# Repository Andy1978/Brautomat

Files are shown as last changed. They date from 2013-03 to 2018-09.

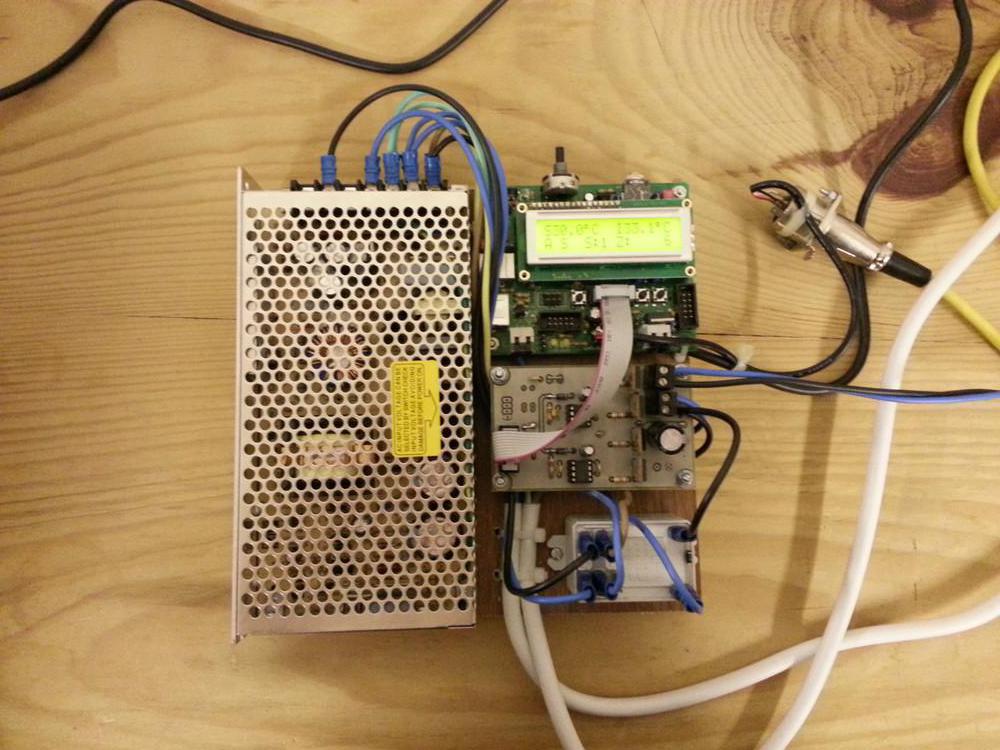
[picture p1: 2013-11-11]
images/detail_ansteuerung.jpg

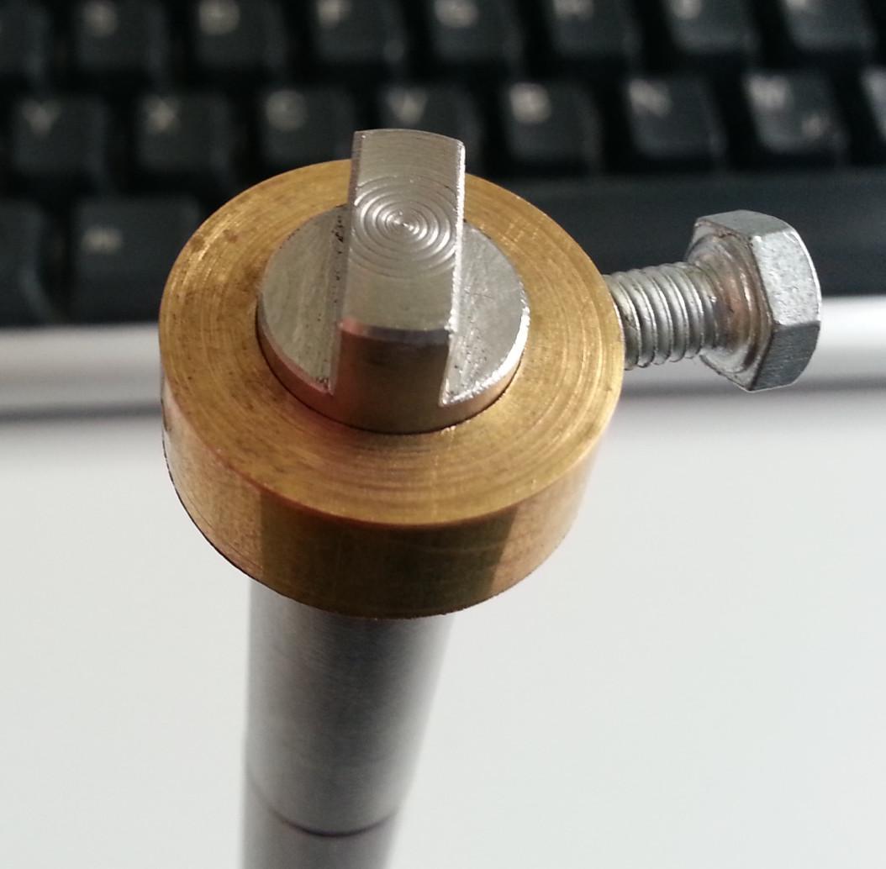
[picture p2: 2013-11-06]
images/edelstahlwelle_zapfen.jpg

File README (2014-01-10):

Brautomat - der (Bier)brau(au)tomat

Funktionen:
  * Ansteuerung des Rührwerks mit konstanter Drehzahl oder Sinusmodulation für maximale Durchmischung
  * Temperaturregelung entlang des konfigurierbaren Profils.

Schaltplände und Stückliste finden sich in /Dokumentation, CAD Zeichnungen kommen noch dazu.
Als  Basis dient YAAMB https://github.com/YAAMB/YAAMB

Bilder finden sich im wiki https://github.com/Andy1978/Brautomat/wiki

ToDo:
  * Wiki strukturieren, Bilder vom Brauprozess
  * CAD Zeichnungen hinzufügen
  * Identifikation der Streckenparameter, siehe playground
  * 2 Punkt Regler in der Software durch quasi kontinuierlichen Regler mit PWM Modulation ersetzen, P oder PI Regler verwenden
  * Neue monolithische Platine mit den wichtigen Komponenten und günstigerer USB<->serial Wandler

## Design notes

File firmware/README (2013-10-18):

*** Brautomat ***

Andreas Weber:
Firmware für den Atmega32 mit MKBoard.
Ich verwende vorerst bei Board mit der HardwareRev1

fuses sind
avrdude -P usb -c usbasp -p atmega32 -U lfuse:w:0x3F:m
avrdude -P usb -c usbasp -p atmega32 -U hfuse:w:0xD9:m

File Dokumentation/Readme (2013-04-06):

02.03.2013 Andreas Weber

Bitte keine Dokumente hinzufügen, für die wir nicht die Rechte haben. Bitte nur verlinken

Atmega32 Datenblatt: www.atmel.com/Images/doc2503.pdf

PT100 Diskussionen
http://www.mikrocontroller.net/topic/183991 (dort von MaWin)
http://groups.google.de/group/de.sci.electronics/browse_thread/thread/6f4a76565e833cb4/6aa603074f212afd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

Nur ganz grobe Werte. (später über Polynom berechnen)
0°C   100R
20°C  108R
100°C 138R

Application Notes:
Precision RTD Instrumentation for Temperature Sensing http://ww1.microchip.com/downloads/en/AppNotes/01154a.pdf ***
Precision Temperature Sensing With RTD Circuits (AN687) ww1.microchip.com/downloads/en/appnotes/00687c.pdf

Für den DS18X20:
http://gandalf.arubi.uni-kl.de/avr_projects/tempsensor/

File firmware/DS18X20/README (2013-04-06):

6.4.2013 Andreas Weber

DS18X20 Library from Martin Thomas
http://www.siwawi.arubi.uni-kl.de/avr_projects/tempsensor/

Makefile und main quick&dirty angepasst für MKBoard und avrdude.

Beispiel hier dient zum auslesen der Seriennummer,
beim ersten gebauten Brautomat (Sensor von Klaus)
SN: 5A F2 BD 04 00 00

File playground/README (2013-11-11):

07.11.2013 Andreas Weber
Spielerei mit octave control

Links:
http://wiki.octave.org/Control_package
http://octave.sourceforge.net/control/index.html
http://web.mit.edu/6.302/www/compare/report.html
http://www.frad.t.u-tokyo.ac.jp/~miyoshi/nu2006/octave-doc-2.1.35/octave_29.html#SEC176

http://www.mathworks.de/de/help/control/index.html

hm, test_control zeigt 2 failed tests.. mal bugreport schreiben?

L = tf(3e4 * [0.0025 0.1 1], [0.01 1.03 3.03 3.01 1]);

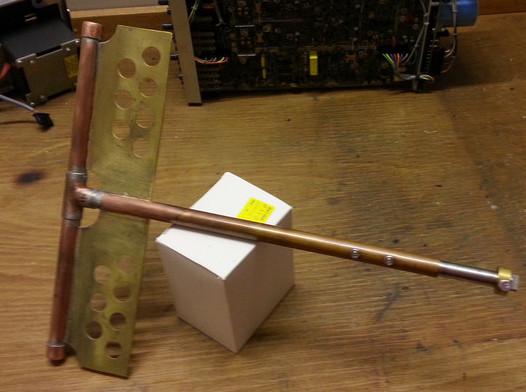
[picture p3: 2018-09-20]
images/ruehrwerk.jpg

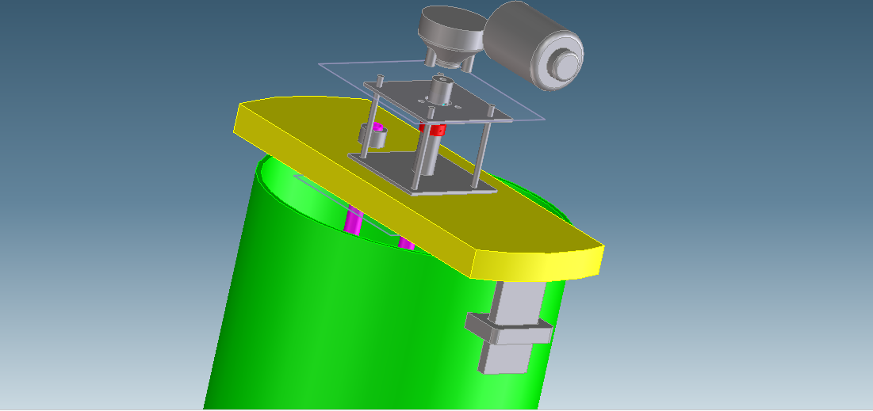
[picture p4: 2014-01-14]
images/cad_detail_motor2.png

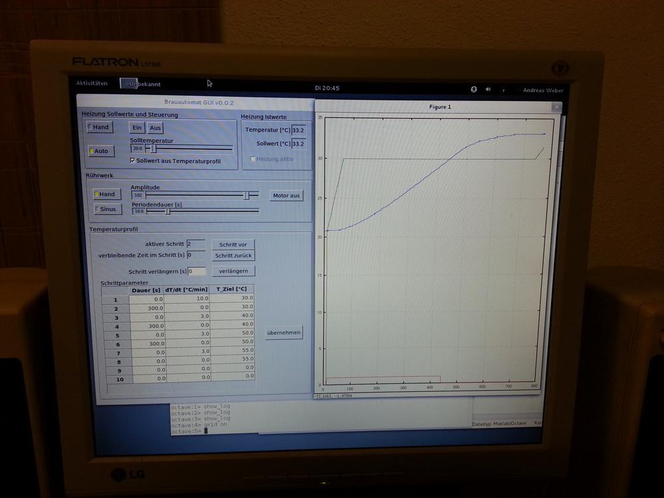
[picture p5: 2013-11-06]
images/screenshot.jpg

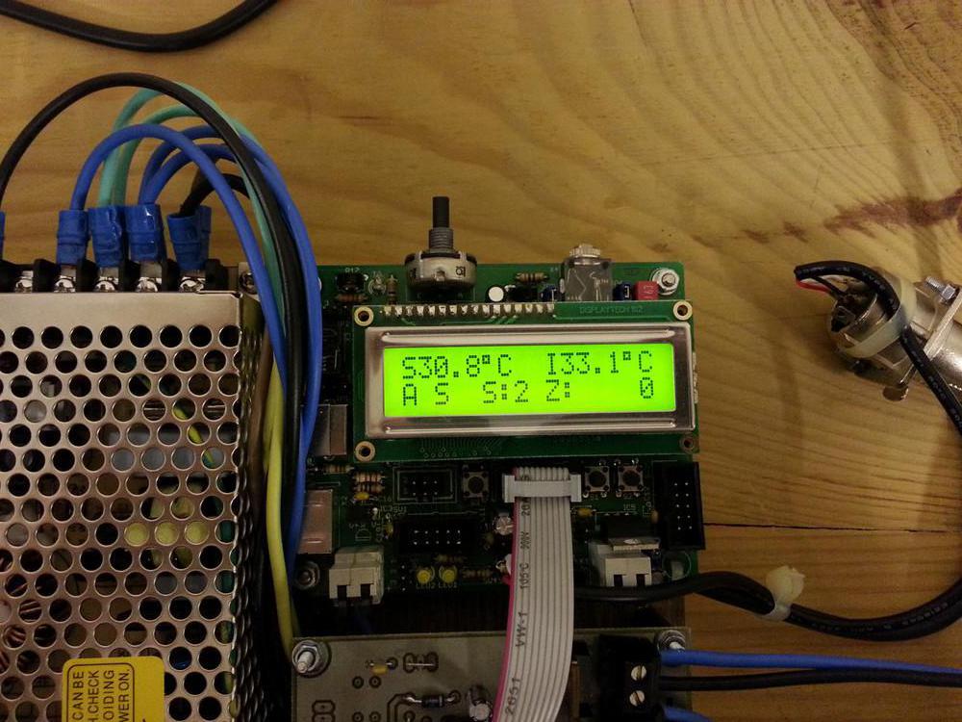
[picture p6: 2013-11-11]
images/detail_lcd.jpg

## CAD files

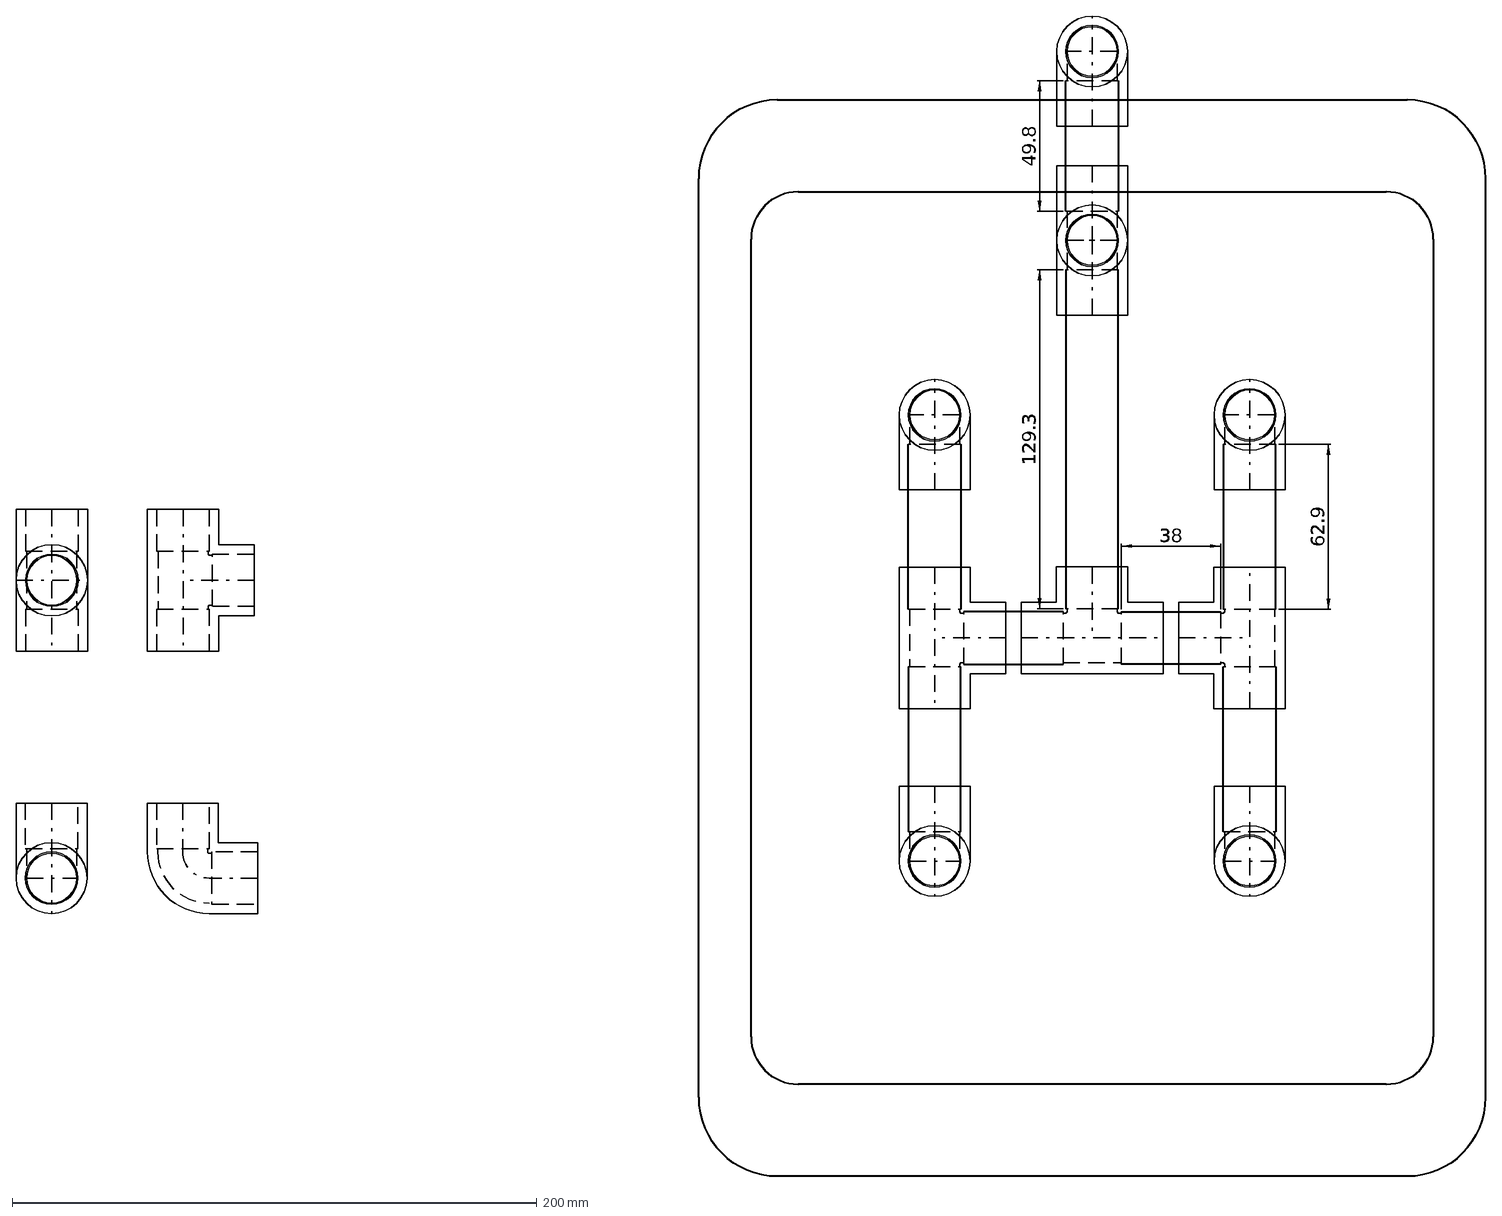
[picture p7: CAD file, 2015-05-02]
CAD/spuelomat.dxf
62.9
38
129.3
49.8

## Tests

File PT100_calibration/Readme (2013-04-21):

19.04.2013 Andreas Weber

Test programs and scripts to test the PT100-wheatstone bridge setup
on AVR differential inputs.

##                               ___    |
##                           5V -UUU----oAVcc
##                                      |
##  .----o--------------o---------------oARef
##  |    |              |               |
##  |   .-.            .-.              |
##  |   | | R1         | | R2           |
##  |   | | 6.8k       | | 6.8k         |
##  |   '-'            '-'              |
##  |    |              |               |
##  |    o--------------)---------------oADC 0
## ---   |              |               |
## ---   |              o---------------oADC 1
##  |    |              |               |
## 100nF |              |               |
##  |   .-.            .-.              |
##  |   | | Rpt        | | R3           |
##  |   | | PT100      | | 120R         |
##  |   '-'            '-'              |
##  |    |              |               |
##  '----o--------------o---------------oAGND
##                                      |
##(created by AACircuit v1.28.6 beta 04/19/05 www.tech-chat.de)

put both sensors (PT100 and DS18B20) into boiling water, run pt100cal with
./pt100cal | tee yourlogfile.log

log the temperature decreasing and then process it in octave

captures/100deg_1.log.gz
  was a first fast polling measurement without timestamp
  and suffered from a int16 overflow (sum filter was too big)

captures/100deg_2.log 
  second capture with temperatures from 95°C .. -5°C (ice and salt)
  huber_D150_2.log is the corresponding, manual captured reference

captures/100deg_3.log 
  third capture in isolated mug and temperatures from 95°C..13.3°C
  huber_D150_3.log is the corresponding, manual captured reference

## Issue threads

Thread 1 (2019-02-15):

Feature Request: Heating-Status-LED and Beep-Sound

Tilogorn, 2019-02-15:
Hi Andy,

i really love your brew automation software! I recently made my first wort with it. Two things would have helped to improve comfort a little:

- would it be possible to get a status LED in the gui, which displays the current state of the heating relay?
- would it be possible to get a beep-sound when the target temperature was reached the first time?

Unfortunately I'm just a webdev and can't create a PR. But be sure to taste one of my "products" some day ;-)

Thanks in advance!
Daniel

Andy1978, 2019-02-15:
There is a checkbox "Heizung aktiv" in the upper right corner which should show the state of the relay. Doesn't work this for you?

For the beep I think we can add some command in the config file which is executed as soon as the temperature is reached. So you can add something as "aplay foobar.wav"
 or "mplayer foobar.mp3"

Tilogorn, 2019-02-19:
> There is a checkbox "Heizung aktiv" in the upper right corner which should show the state of the relay. Doesn't work this for you?

That's exactly what I was looking for. I am blind sometimes. Thanks a lot.

> For the beep I think we can add some command in the config file which is executed as soon as the temperature is reached. So you can add something as "aplay foobar.wav"
> or "mplayer foobar.mp3"

Sounds like a very flexible solution!. One can play sounds, send mails, set GPIOs (Rpi) or whatever ...

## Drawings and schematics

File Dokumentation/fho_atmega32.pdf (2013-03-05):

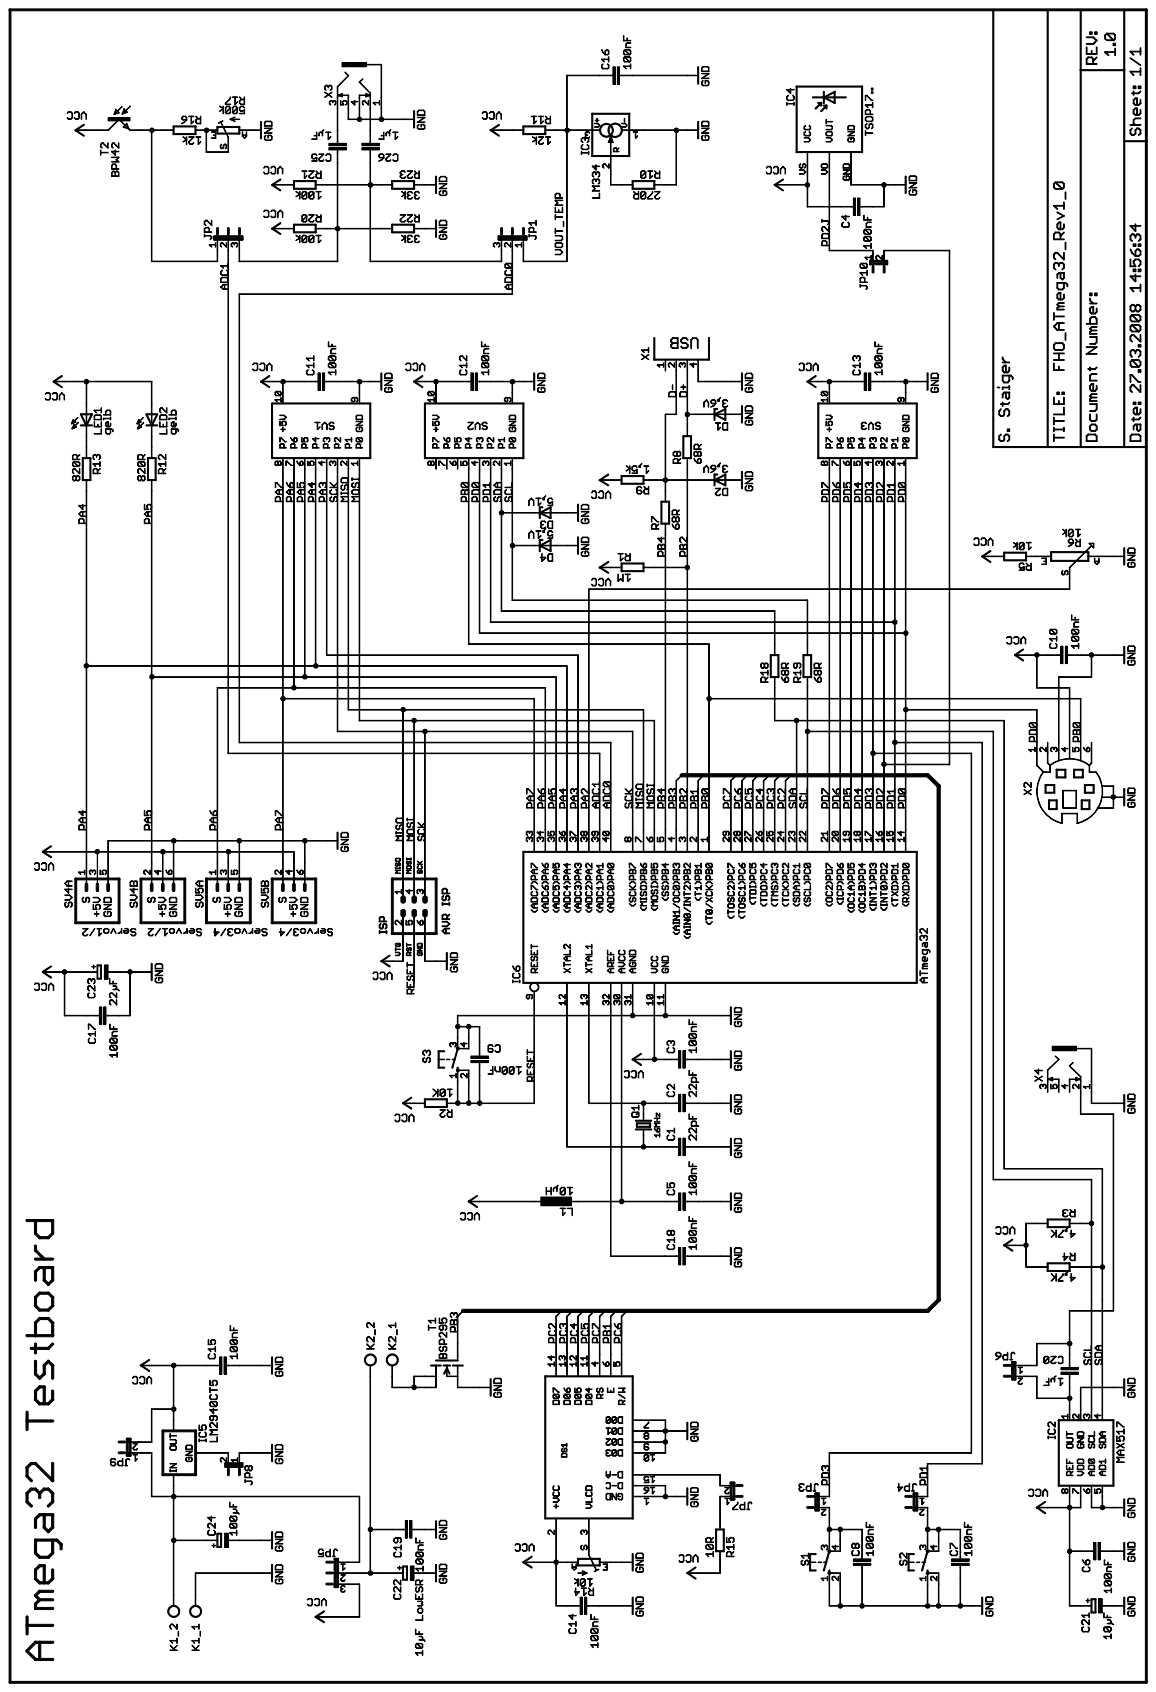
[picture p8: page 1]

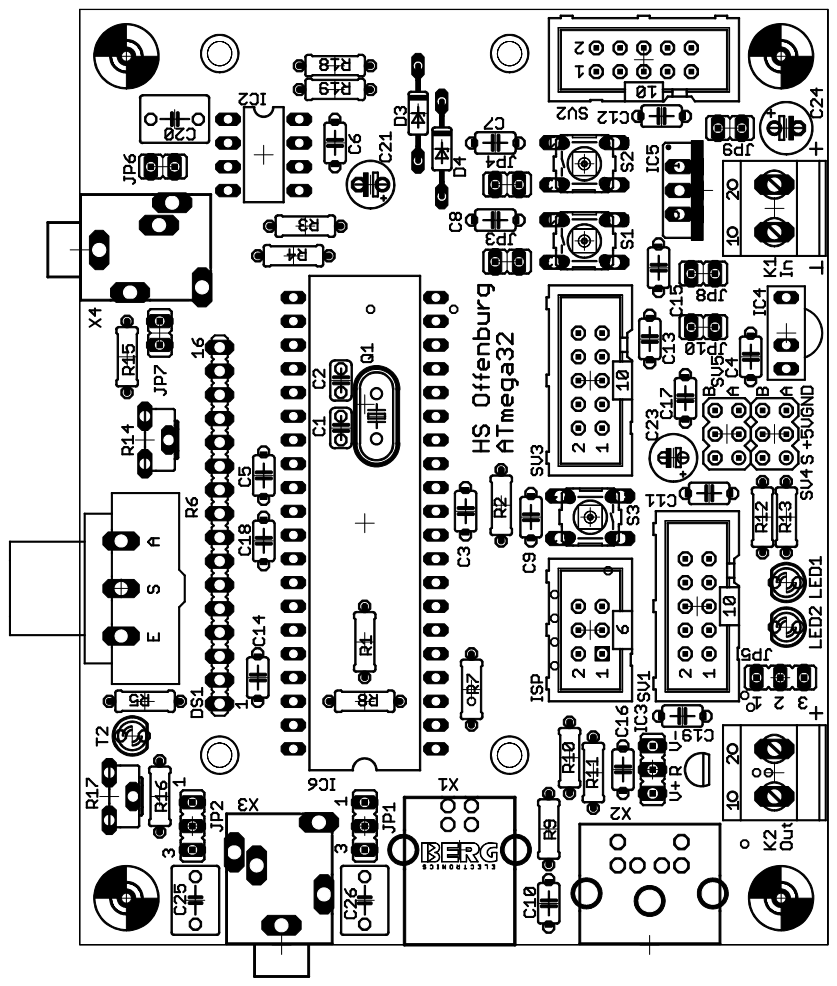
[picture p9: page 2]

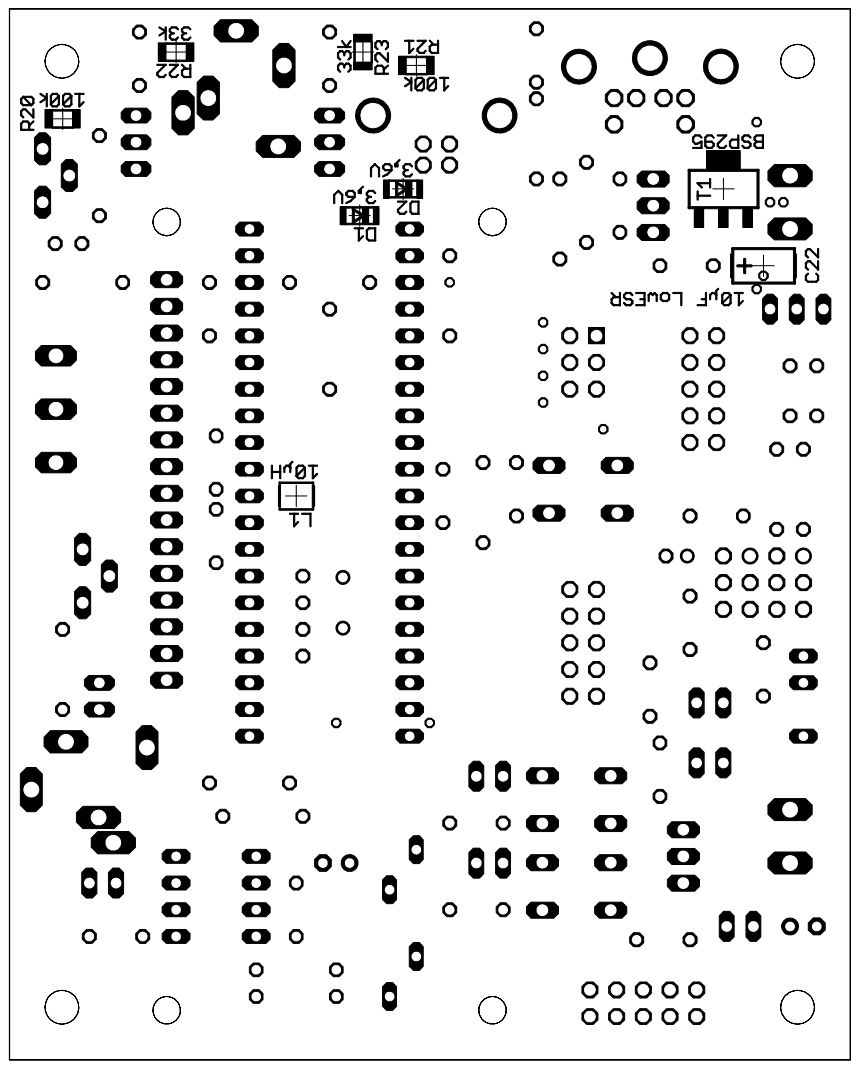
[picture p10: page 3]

Tabelle1

Seite 1

Menge Part

2 | C1, C2 | 22pF | C025-024X044
17 | C3-C19 | 100nF | C050-024X044
3 | C20, C25, C26 | 1µF | C050-050X075
1 | C21 | 10µF | E2,5-5
1 | C22 | | CT6032 (SMD)
1 | C23 | 22µF | E2-5
1 | C24 | 100µF | E2,5-6
1 | R1 | 1M | 0207/7
2 | R2, R5 | 10k | 0207/7
2 | R3, R4 | 4,7k | 0207/7
1 | R6 | 10k | P6M-S (Poti)
4 | R7, R8, R18, R19 | 68R | 0207/7
1 | R9 | 1,5k | 0207/7
1 | R10 | 270R | 0207/7
2 | R11, R16 | 12k | 0207/7
2 | R12, R13 | 820R | 0207/7
1 | R14 | 10k | CA6H (Poti)
1 | R15 | 10R | 0207/7
1 | R17 | 500k | CA6H (Poti)
2 | R20, R21 | 100k | R1206 (SMD)
2 | R22, R23 | 33k | R1206 (SMD)
2 | D1, D2 | 3,6V | SOD80C (SMD)
2 | D3, D4 | 5,1V | DO35Z10
2 | LED1, LED2 | LED gelb 3mm | LED3MM
1 | DS1 | LCD 162C LED | HDM20216H_OHNE
1 | IC1 | MEGA32-P | DIL40
1 | IC2 | MAX517 | DIL08
1 | IC3 | LM334 | JP2Y
1 | IC4 | TSOP17.. | TSOP17..
1 | IC5 | LM2940CT5 | 78XXS
1 | T1 | BSP295 | SOT223
1 | T2 | BPW42 | FOTOTRAN3MM
3 | SV1-SV3 | Wannenstecker 10pol | ML10
3 | ISP, SV4, SV5 | Stiftleiste 2reihig 6polig | MA03-2
3 | JP1, JP2, JP5 | Jumper 3polig | JP2
7 | JP3, JP4, JP6-JP10 Jumper 2polig | JP1
2 | K1, K2 | Klemme 2polig | AKL073-02
3 | S1-S3 | Taster | B3F-10XX
1 | X1 | USB B Stecker | USB_B_STECKER
1 | X2 | PS2 Buchse | PS2
2 | X3, X4 | | STEREO_MIT_SCHALTER
1 | L1 | Induktivität 10µH | L3230M (SMD)
1 | Q1 | Quarz 16MHz | HC49U-V
Value | Package

10µF LowESR

Klinkenbuchse 3,5mm stereo

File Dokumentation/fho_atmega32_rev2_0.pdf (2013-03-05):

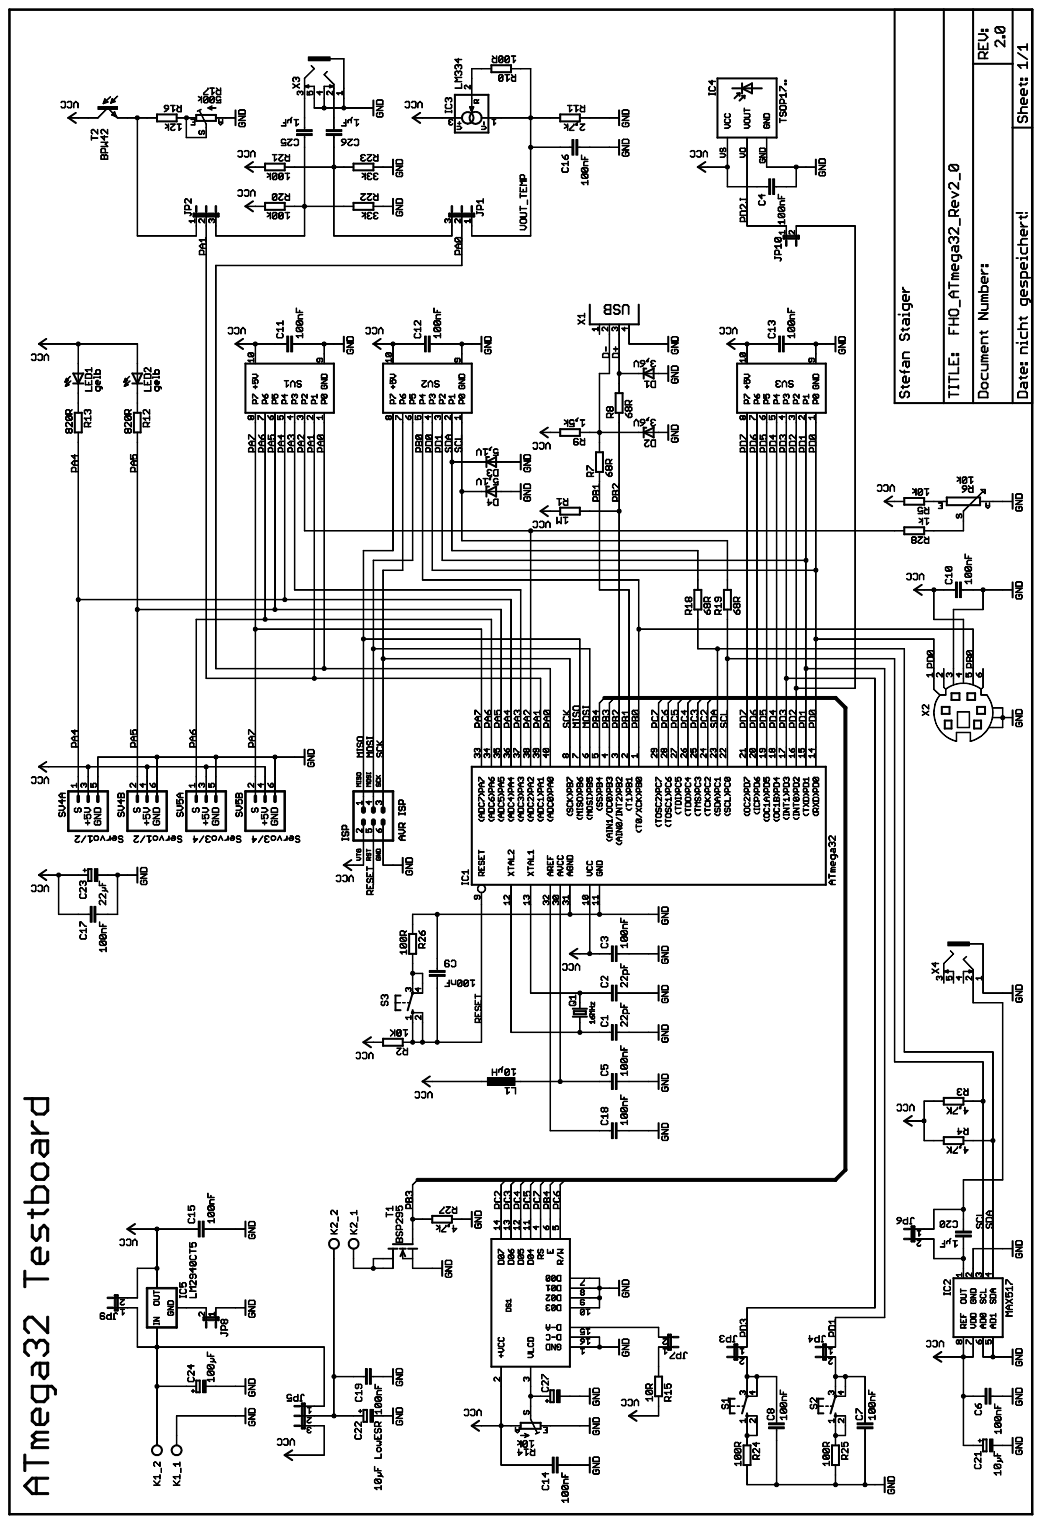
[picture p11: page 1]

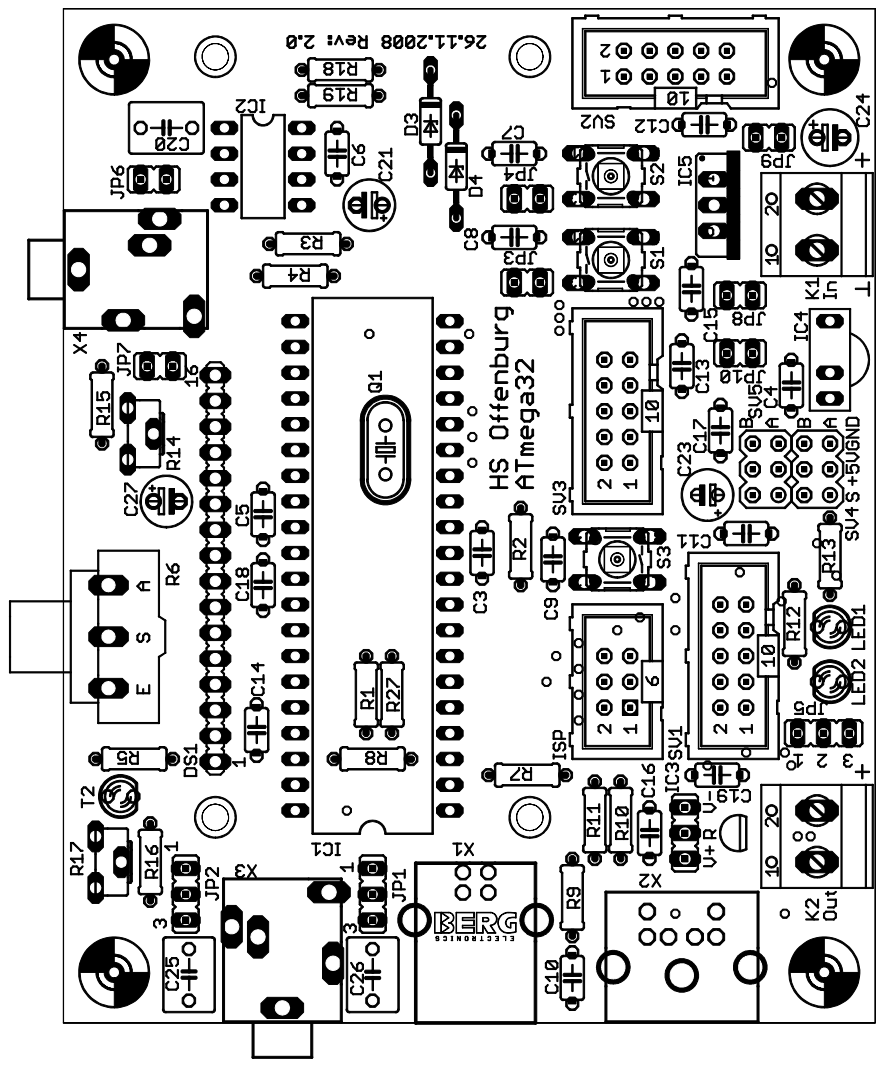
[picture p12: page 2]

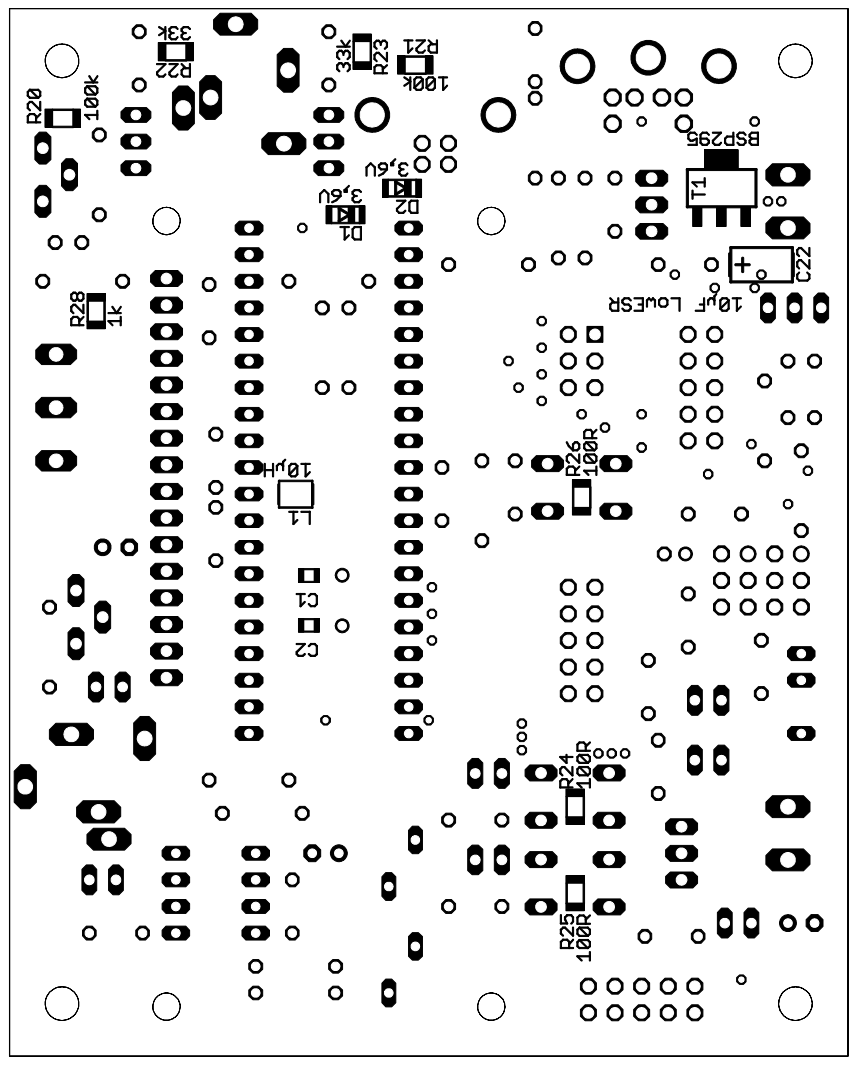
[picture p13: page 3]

Partlist

| Part | Value | Package
2 | C1, C2 | 22pF | C0805k (SMD)
17 | C3-C19 | 100nF | C050-024X044
3 | C20, C25, C26 | 1µF | C050-050X075
1 | C21 | 10µF | E2,5-5
1 | C22 | | CT6032 (SMD)
1 | C23 | 22µF | E2-5
1 | C24 | 100µF | E2,5-6
1 | C27 | 1µF | E2,5-5
1 | R1 | 1M | 0207/7
2 | R2, R5 | 10k | 0207/7
3 | R3, R4, R27 | 4,7k | 0207/7
1 | R6 | 10k
4 | R7, R8, R18, R19 | 68R | 0207/7
1 | R9 | 1,5k | 0207/7
1 | R10 | 100R | 0207/7
1 | R11 | 2,7k | 0207/7
2 | R12, R13 | 820R | 0207/7
1 | R14 | 10k
1 | R15 | 10R | 0207/7
1 | R16 | 12k | 0207/7
1 | R17 | 500k
2 | R20, R21 | 100k | R1206 (SMD)
2 | R22, R23 | 33k | R1206 (SMD)
2 | R24, R25, R26 | 100R | R1206 (SMD)
1 | R28 | 1k | R1206 (SMD)
2 | D1, D2 | Z-Diode 3,6V | SOD80C (SMD)
2 | D3, D4 | Z-Diode 5,1V | DO35Z10
2 | LED1, LED2 | | LED3MM
1 | DS1 | | HDM20216H_OHNE
1 | IC1 | MEGA32-P | DIL40
1 | IC2 | MAX517 | DIL08
1 | IC3 | LM334 | JP2Y
1 | IC4 | TSOP1736 | TSOP17..
1 | IC5 | LM2940CT5 | 78XXS
1 | T1 | BSP295 | SOT223 (SMD)
1 | T2 | BPW42 | FOTOTRAN3MM
3 | SV1-SV3 | | ML10
3 | ISP, SV4, SV5 | | MA03-2
3 | JP1, JP2, JP5 | | JP2
7 | JP3, JP4, JP6-JP10 | | JP1
1 | | | JP2Y
2 | K1, K2 | | AST 025-02
3 | S1-S3 | Taster | B3F-10XX
1 | X1 | | USB_B_STECKER
1 | X2 | | PS2
2 | X3, X4
1 | L1 | 10µH | L3230M (SMD)
1 | Q1 | | HC49U-V

Menge

10µF LowESR

P6M-S (Poti)

CA6H (Poti)

CA6H (Poti)

LED gelb 3mm
LCD 2x16 Zeichen

Wannstecker 10pol
Stiftleiste 2reihig 6polig Stiftleiste 1reihig 3polig Stiftleiste 1reihig 2polig
Buchse für IC3 | Buchsenleiste 3polig
Klemme 2polig

USB B Stecker
PS2 Buchse
Klinkenbuchse 3,5mm stereo Klinkenbuchse

Quarz 16MHz

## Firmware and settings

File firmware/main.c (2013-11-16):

/*
    Copyright 2013 Andreas Weber (andy.weber.aw at gmail dot com)

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
    You should have received a copy of the GNU General Public License
    along with this program.  If not, see <http://www.gnu.org/licenses/>.
*/

/*************************************************

  Brautomat AVR firmware

  Autor: Andreas Weber
  src: https://github.com/Andy1978/Brautomat
  changelog: 02.03.2013 angelegt
             06.04.2013 aw: PT100 nun über Wheatstone Brücke einlesen und DS18B20
             22.10.2013 aw: PT100 entfernt, nur noch DS18B20

  Infos:
  H-Brücken PWM Treiber IR2104
  IN obere Halbbrücke PD4, OC1B
  /SD obere Halbbrücke PD6
  IN untere Halbbrücke PD5, OC1A
  /SD untere Halbbrücke PD7

  Scheibenwischermotor Opel Astra Bj 86..89?
  Stecker-Pin Adernfarbe  Funktion
  E           weiß        Motor schnell gegen Masse/Gehäuse
  D           violett/sw  0-Stellung
  C           grün        0-Stellung kurz gegen MAsse
  B
  A           orange      Motor langsam gegen Masse/Gehäuse

  Relais für Heizung: PB3

  Maxim DS18B20 an PA6, externe Versorgung 4,7k Pull-Up

  LCD:
  S99.5°C  I77.3°C
  RH....

  Buchstaben links in der unteren Zeile zeigen:
  Zeichen
  1: A = Temperaturegelung aktiv
     M = Heizung im manuellen(Hand-) Betrieb
  2: H = Heizung an
    ' '= Heizung aus
  3: S = Temperatursollwerte aus Schrittkette
    ' '=

**************************************************/

#define USE_LCD

#include <stdlib.h>
#include <string.h>
#include <stdio.h>
#include <avr/io.h>
#include <avr/interrupt.h>
#include <avr/pgmspace.h>
#include <util/delay.h>
#ifdef USE_LCD
#include "lcd.h"
#endif
#include "uart.h"
#include "onewire.h"
#include "ds18x20.h"

#define MAX_STEPS 10

//Telegramm AVR zum PC
struct s_status
{
  float temperature;            //Isttemperatur von DS18B20[°C]
  float temperature_set_point;  //Solltemperatur [°C]
  uint8_t aktive_step;          //aktueller Schritt im Ablauf
  uint16_t remaining_step_time; //verbleibende Zeit im aktuellen Schritt [s]
  uint8_t  bits;
  //Bit 0 H: Heizung aktiv
  uint8_t uart_error_cnt;
  uint8_t last_uart_error;
};

//Telegramm vom PC zum AVR
struct s_setvalues
{
  float temperature_set_point;  //Solltemperatur [°C]
  int8_t amplitude_set_point;  //Amplitude Rührwerk -127..126
  uint8_t period_set_point;     //Periodendauer Rührwerk in 100ms (0=keine Modulation)
  float step_temp[MAX_STEPS];   //Temperatur in der Schrittkette [°C]
  float dT_dt[MAX_STEPS];       //Temperaturanstieg [°C/min]
  uint16_t step_time[MAX_STEPS]; //Dauer Schritt [s]
  uint16_t add_to_remaining_step_time; //wird zu remaining_step_time
  uint8_t	 bits;
  //Bit 0: Temperaturregelung aktiv (Handbetrieb wenn nicht)
  //Bit 1: Heizung aktiv im Handbetrieb
  //Bit 2: Temperatursollwerte aus Schrittkette
  //Bit 3: Schritt weiter (Flanke)
  //Bit 4: Schritt zurück (Flanke)
};

#define UART_BAUD_RATE 38400
//#define UART_BAUD_RATE 115200
#define OW_ONE_BUS

#define HYSTERTESE 0.2

volatile struct s_status status;
volatile struct s_setvalues setvalues;
volatile uint8_t do_ds18b20_meas;
volatile uint8_t do_update_lcd;

uint8_t uart_error;
uint8_t gSensorID[OW_ROMCODE_SIZE]={ 0x5A, 0xF2, 0xBD, 0x04};

// sin_list generated with octave:
// p=linspace(0,2*pi,33); p(end)=[];
// printf("%i,",fix(sin(p)*511))
// int16_t sin_list[]={0,99,195,283,361,424,472,501,511,501,472,424,361,283,195,99,0,-99,-195,-283,-361,-424,-472,-501,-511,-501,-472,-424,-361,-283,-195,-99};

// p=linspace(0,2*pi,65); p(end)=[];
// printf("%.4f,",sin(p)*4)
float sin_list[]={0.0000,0.3921,0.7804,1.1611,1.5307,1.8856,2.2223,2.5376,2.8284,3.0920,3.3259,3.5277,3.6955,3.8278,3.9231,3.9807,4.0000,3.9807,3.9231,3.8278,3.6955,3.5277,3.3259,3.0920,2.8284,2.5376,2.2223,1.8856,1.5307,1.1611,0.7804,0.3921,0.0000,-0.3921,-0.7804,-1.1611,-1.5307,-1.8856,-2.2223,-2.5376,-2.8284,-3.0920,-3.3259,-3.5277,-3.6955,-3.8278,-3.9231,-3.9807,-4.0000,-3.9807,-3.9231,-3.8278,-3.6955,-3.5277,-3.3259,-3.0920,-2.8284,-2.5376,-2.2223,-1.8856,-1.5307,-1.1611,-0.7804,-0.3921};

#ifdef USE_LCD
//  Integer (Basis 10) rechtsbündig auf LCD ausgeben.
void lcd_put_int(int16_t val, uint8_t len)
{
  char buffer[len+1];
  itoa(val,buffer,10);
  size_t empty=len-strlen(buffer);
  while(empty--)
    lcd_putc(' ');
  lcd_puts(buffer);
}

void lcd_put_int32(int32_t val, uint8_t len)
{
  char buffer[len+1];
  ltoa(val,buffer,10);
  size_t empty=len-strlen(buffer);
  while(empty--)
    lcd_putc(' ');
  lcd_puts(buffer);
}

void update_lcd(void)
{

  char buf[20];

  //Solltemperatur
  lcd_gotoxy(0,0);
  _delay_ms(1);   //sonst zickt gotoxy rum, TODO: nachprüfen, ggf. Zeit verkleinern
  lcd_puts_P("S");
  dtostrf(status.temperature_set_point,4,1,buf);
  lcd_puts(buf);
  lcd_putc(0xDF);
  lcd_putc('C');

  //Isttemperatur
  //lcd_gotoxy(0,1);
  lcd_puts_P("  I");
  dtostrf(status.temperature,4,1,buf);
  lcd_puts(buf);
  lcd_putc(0xDF);
  lcd_putc('C');

  //Status
  lcd_putc((setvalues.bits & _BV(0))? 'A':'M');
  lcd_putc((status.bits & _BV(0))? 'H':' ');
  lcd_putc((setvalues.bits & _BV(2))? 'S':' ');
  lcd_putc(' ');

  //aktiver Schritt
  lcd_puts_P(" S:");
  itoa(status.aktive_step,buf,10);
  lcd_puts(buf);

  //verbleibende Zeit im Schritt in Sekunden
  sprintf(buf," Z:%5i",status.remaining_step_time);
  lcd_puts(buf);

/*
  lcd_gotoxy(0,0);
  lcd_put_int(status.uart_error_cnt,3);
  lcd_putc(' ');
  lcd_put_int(uart_error,3);
*/

}
#endif
//ISR(TIMER0_COMP_vect, ISR_NOBLOCK) //1kHz
ISR(TIMER0_COMP_vect) //1kHz
{
  static int16_t cnt=0;
  static uint16_t ruehr_cnt=0;
  static uint8_t sin_index=0;
  static uint16_t temp_cnt=0;
  if (cnt++ == 500)
  {
    do_ds18b20_meas=1;
    cnt = 0;
  }
  else if(cnt==250)
  {
    do_update_lcd=1;
  }

  if(setvalues.period_set_point==0) //Handbetrieb
  {
    OCR1A=512-setvalues.amplitude_set_point*4;
    OCR1B=512+setvalues.amplitude_set_point*4;
    sin_index = 0;
  }
  else
  {
    if(ruehr_cnt++ > (3*setvalues.period_set_point+setvalues.period_set_point/8)) //>3.125*period
    {
      ruehr_cnt = 0;
      if(++sin_index>63)
        sin_index=0;
      float f = sin_list[sin_index] * setvalues.amplitude_set_point;
      OCR1A=512 - f;
      OCR1B=512 + f;
    }
  }

  //Heizungsregelung
  //Quelle des Sollwerts?
  //Schrittzähler
  static uint8_t last_next_step = 0;
  static uint8_t last_previous_step = 0;
  static uint8_t last_temp_from_profile = 0;
  static uint16_t last_add_to_remaining_step_time = 0;

  //positive Flanke Temperatur aus Temperaturprofile setzt Schrittzähler zurück
  if(setvalues.bits & _BV(2) && !last_temp_from_profile)
  {
    status.aktive_step = 0;
    status.temperature_set_point = status.temperature;
    status.remaining_step_time = setvalues.step_time[status.aktive_step];
  }
  last_temp_from_profile = setvalues.bits & _BV(2);

  //soll ein Wert zur remaining_step_time adiiert werden?
  if(setvalues.add_to_remaining_step_time != last_add_to_remaining_step_time)
    status.remaining_step_time += setvalues.add_to_remaining_step_time;
  last_add_to_remaining_step_time = setvalues.add_to_remaining_step_time;

  if(setvalues.bits & _BV(2)) //aus dem Temperaturprofile
  {
    if((setvalues.bits & _BV(3)) && !last_next_step)  //Schritt vor
    {
      status.aktive_step++;
      status.remaining_step_time = setvalues.step_time[status.aktive_step];
    }
    last_next_step = setvalues.bits & _BV(3);

    if((setvalues.bits & _BV(4)) && !last_previous_step)  //Schritt zurück
    {
      status.aktive_step--;
      status.remaining_step_time = setvalues.step_time[status.aktive_step];
    }
    last_previous_step = setvalues.bits & _BV(4);

    //auf Sekunden runter teilen
    if(temp_cnt++ > 1000)
    {
      temp_cnt=0;
      float tmp_dT_dt = setvalues.dT_dt[status.aktive_step]/60.0;
      float delta_T = setvalues.step_temp[status.aktive_step]-status.temperature_set_point ;
      if(tmp_dT_dt == 0.0)
        status.temperature_set_point = setvalues.step_temp[status.aktive_step];
      else if(tmp_dT_dt>0)
      {
        if(tmp_dT_dt>delta_T)
          tmp_dT_dt = delta_T;

        if(status.temperature_set_point < setvalues.step_temp[status.aktive_step])
          status.temperature_set_point += tmp_dT_dt;

        if(status.temperature >= setvalues.step_temp[status.aktive_step])
        {
          status.aktive_step++;
          status.remaining_step_time = setvalues.step_time[status.aktive_step];
        }
      }
      else
      {
        if(tmp_dT_dt<delta_T)
          tmp_dT_dt = delta_T;

        if(status.temperature_set_point > setvalues.step_temp[status.aktive_step])
          status.temperature_set_point += tmp_dT_dt;

        if(status.temperature < setvalues.step_temp[status.aktive_step])
        {
          status.aktive_step++;
          status.remaining_step_time = setvalues.step_time[status.aktive_step];
        }
      }

      //über Zeit zum nächsten Schritt schalten?
      if(status.remaining_step_time>0)
        status.remaining_step_time--;
      else if(setvalues.step_time[status.aktive_step]>0)
      {
        status.aktive_step++;
        status.remaining_step_time = setvalues.step_time[status.aktive_step];
      }
    }
  }
  else //von temperature_set_point
  {
    status.temperature_set_point = setvalues.temperature_set_point;
  }

  if(setvalues.bits & _BV(0))  //Temperaturregelung aktiv?
  {
    if(status.temperature >= status.temperature_set_point)
     status.bits &= 0xFE;
    else if(status.temperature < (status.temperature_set_point-HYSTERTESE))
     status.bits |= 1;
  }
  else  //Hand
  {
    if(setvalues.bits & _BV(1))
     status.bits |= 1;
    else
     status.bits &= 0xFE;
  }

  //Heizung ein/ausschalten anhand von status
  if(status.bits & _BV(0))
    PORTB |= _BV(PB3);
  else
    PORTB &= ~(_BV(PB3));
}

ISR(ADC_vect) //ca. 125kHz
{
  //momentan keine Verwendung für den ADC
  //int16_t temp=ADC-512;
  //~ OCR1A=512-temp;
  //~ OCR1B=512+temp;
}

// UART bearbeiten. Es gibt nur ein Telegramm mit allen Sollwerten
// und eine Antwort mit allen Istwerten bzw. Status
void processUART(void)
{
  //Alle Daten empfangen
  while(uart_GetRXCount()>=sizeof(struct s_setvalues))
  {
    //Empfangen
    char* rec=(char*)&setvalues;
    uint8_t i;
    uint16_t rx_tmp;
    for(i=0;i<sizeof(struct s_setvalues);i++)
    {
      rx_tmp=uart_getc();
      rec[i]=rx_tmp & 0xFF;
      if(rx_tmp & 0xFF00)
      {
        status.uart_error_cnt++;
        uart_error=((rx_tmp & 0xFF00) >> 8);
      }
    }
    //status.bits |= setvalues.bits;
    //Senden
    char* send=(char*)&status;
    for(i=0;i<sizeof(struct s_status);i++)
    {
      uart_putc(send[i]);
    }
  }
}

int main(void)
{
  //uart_init(UART_BAUD_SELECT_DOUBLE_SPEED(UART_BAUD_RATE,F_CPU));
  uart_init(UART_BAUD_SELECT(UART_BAUD_RATE,F_CPU));
#ifdef USE_LCD
  lcd_init(LCD_DISP_ON);
  lcd_clrscr();
  lcd_puts_P("Brautomat v0.6\n");
  lcd_gotoxy(0,1);
  lcd_puts_P(__DATE__" aw");

  //3s Delay for Splash
  for(uint8_t i=0;i<200;++i)
    _delay_ms(15);
  lcd_clrscr();
#endif

  //H-Brücke
  DDRD |= _BV(PD2) | _BV(PD4) | _BV(PD5) | _BV(PD6) | _BV(PD7);
  //Relais für Heizung
  DDRB |= _BV(PB3);
  PORTD |= _BV(PD6) | _BV(PD7);

  /*** TIMER0 ***/
  OCR0=250;
  //CTC = Clear Timer on Compare match S.80
  //Normal port operation, OC0 disconnected
  //Prescaler=64 -> clk=250kHz
  TCCR0 = _BV(WGM01) | _BV(CS01) | _BV(CS00);
  //On Compare match Interrupt Enable for timer 0
  TIMSK |= _BV(OCIE0);

  /** TIMER1 **/
  //PWM Phase correct 10bit
  //Set OC1A+OC1B on match when upcounting (page 108)
  TCCR1A = _BV(COM1A1) | _BV(COM1B1) | _BV(COM1A0) | _BV(COM1B0) | _BV(WGM11) | _BV(WGM10);
  //Prescaler = 1 (page 110)
  TCCR1B = _BV(CS10);


  /*** ADC ***/
  //Prescaler 128 = 125kHz ADC Clock, AutoTrigger, Interrupts enable
  ADCSRA = _BV(ADEN) | _BV(ADPS0) | _BV(ADPS1) | _BV(ADPS2) | _BV(ADATE) | _BV(ADSC) | _BV(ADIE);

  //AVCC with external capacitor at AREF, internal 2.56V bandgap
  //siehe S. 215
  ADMUX = (_BV(REFS0) | _BV(REFS1)) + 2;
  //ADC in Free Running mode
  SFIOR &= ~(_BV(ADTS2) | _BV(ADTS1) | _BV(ADTS0));

  //DS18B20 an PA6
  ow_set_bus(&PINA,&PORTA,&DDRA,PA6);

  //enable global interrupts
  sei();

  for (;;)    /* main event loop */
    {
      processUART();
      if(do_ds18b20_meas)
      {
        //Temperatur am DS18B20 messen
        // zwischen DS18X20_start_meas und DS18X20_read_decicelsius_single
        // muß _delay_ms( DS18B20_TCONV_12BIT ); (750ms) gewartet werden.
        // alte Messung lesen
        int16_t decicelsius;
        DS18X20_read_decicelsius_single( gSensorID[0], &decicelsius );
        status.temperature = decicelsius/10.0;
        //neue Messung starten
        //DS18X20_start_meas( DS18X20_POWER_PARASITE, NULL );
        DS18X20_start_meas( DS18X20_POWER_EXTERN, NULL );
        do_ds18b20_meas = 0;
      }
#ifdef USE_LCD
      if(do_update_lcd)
      {
        update_lcd();
        do_update_lcd=0;
      }
#endif
    }
    return 0;
}

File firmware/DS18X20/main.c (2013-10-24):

/*
   DS18x20 Demo-Program

   V 0.9.2, 2/2011

   by Martin Thomas <eversmith@heizung-thomas.de>
   http://www.siwawi.arubi.uni-kl.de/avr-projects

   features:
   - DS18X20 and 1-Wire code is based on an example from Peter
     Dannegger
   - uses Peter Fleury's uart-library which is very portable
   - additional functions not found in the  uart-lib available
     in uart.h/.c
   - CRC-check based on code from Colin O'Flynn
   - accesses multiple sensors on multiple 1-Wire busses
   - example how to address every sensor in the bus by ROM-code
   - independant of system-timers (more portable) but some
     (very short) delays used
   - avr-libc's stdint.h in use
   - no central include-file, parts of the code can be used as
     "library" easily
   - verbose output example
   - one-wire-bus can be changed at runtime if OW_ONE_BUS
     is not defined in onewire.h. There are still minor timing
     issues when using the dynamic bus-mode
   - example on read/write of DS18x20 internal EEPROM
*/


/* This example has been tested with ATmega324P at 3.6864MHz and 16Mhz */


#include <avr/version.h>
#if __AVR_LIBC_VERSION__ < 10606UL
#error "please update to avrlibc 1.6.6 or newer, not tested with older versions"
#endif


#include <avr/io.h>
#include <avr/pgmspace.h>
#include <avr/interrupt.h>
#include <avr/eeprom.h>
#include <util/delay.h>
#include <string.h>
#include <stdint.h>

#include "uart.h"
#include "uart_addon.h"
#include "onewire.h"
#include "ds18x20.h"

#define BAUD 19200
// 2400 for 1MHz and 2MHz internal RC
// #define BAUD 2400

#define MAXSENSORS 5

#define NEWLINESTR "\r\n"


uint8_t gSensorIDs[MAXSENSORS][OW_ROMCODE_SIZE];


static uint8_t search_sensors(void)
{
	uint8_t i;
	uint8_t id[OW_ROMCODE_SIZE];
	uint8_t diff, nSensors;

	uart_puts_P( NEWLINESTR "Scanning Bus for DS18X20" NEWLINESTR );

	ow_reset();

	nSensors = 0;

	diff = OW_SEARCH_FIRST;
	while ( diff != OW_LAST_DEVICE && nSensors < MAXSENSORS ) {
		DS18X20_find_sensor( &diff, &id[0] );

		if( diff == OW_PRESENCE_ERR ) {
			uart_puts_P( "No Sensor found" NEWLINESTR );
			break;
		}

		if( diff == OW_DATA_ERR ) {
			uart_puts_P( "Bus Error" NEWLINESTR );
			break;
		}

		for ( i=0; i < OW_ROMCODE_SIZE; i++ )
			gSensorIDs[nSensors][i] = id[i];

		nSensors++;
	}

	return nSensors;
}

static void uart_put_temp(int16_t decicelsius)
{
	char s[10];

	uart_put_int( decicelsius );
	uart_puts_P(" deci°C, ");
	DS18X20_format_from_decicelsius( decicelsius, s, 10 );
	uart_puts( s );
	uart_puts_P(" °C");
}


#if DS18X20_MAX_RESOLUTION

static void uart_put_temp_maxres(int32_t tval)
{
	char s[10];

	uart_put_longint( tval );
	uart_puts_P(" °Ce-4, ");
	DS18X20_format_from_maxres( tval, s, 10 );
	uart_puts( s );
	uart_puts_P(" °C");
}

#endif /* DS18X20_MAX_RESOLUTION */


#if DS18X20_EEPROMSUPPORT

static void th_tl_dump(uint8_t *sp)
{
	DS18X20_read_scratchpad( &gSensorIDs[0][0], sp, DS18X20_SP_SIZE );
	uart_puts_P( "TH/TL in scratchpad of sensor 1 now : " );
	uart_put_int( sp[DS18X20_TH_REG] );
	uart_puts_P( " / " );
	uart_put_int( sp[DS18X20_TL_REG] );
	uart_puts_P( NEWLINESTR );
}

static void eeprom_test(void)
{
	uint8_t sp[DS18X20_SP_SIZE], th, tl;

	uart_puts_P( NEWLINESTR "DS18x20 EEPROM support test for first sensor" NEWLINESTR );
	// DS18X20_eeprom_to_scratchpad(&gSensorIDs[0][0]); // already done at power-on
	th_tl_dump( sp );
	th = sp[DS18X20_TH_REG];
	tl = sp[DS18X20_TL_REG];
	tl++;
	th++;
	DS18X20_write_scratchpad( &gSensorIDs[0][0], th, tl, DS18B20_12_BIT );
	uart_puts_P( "TH+1 and TL+1 written to scratchpad" NEWLINESTR );
	th_tl_dump( sp );
	DS18X20_scratchpad_to_eeprom( DS18X20_POWER_PARASITE, &gSensorIDs[0][0] );
	uart_puts_P( "scratchpad copied to DS18x20 EEPROM" NEWLINESTR );
	DS18X20_write_scratchpad( &gSensorIDs[0][0], 0, 0, DS18B20_12_BIT );
	uart_puts_P( "TH and TL in scratchpad set to 0" NEWLINESTR );
	th_tl_dump( sp );
	DS18X20_eeprom_to_scratchpad(&gSensorIDs[0][0]);
	uart_puts_P( "DS18x20 EEPROM copied back to scratchpad" NEWLINESTR );
	DS18X20_read_scratchpad( &gSensorIDs[0][0], sp, DS18X20_SP_SIZE );
	if ( ( th == sp[DS18X20_TH_REG] ) && ( tl == sp[DS18X20_TL_REG] ) ) {
		uart_puts_P( "TH and TL verified" NEWLINESTR );
	} else {
		uart_puts_P( "verify failed" NEWLINESTR );
	}
	th_tl_dump( sp );
}
#endif /* DS18X20_EEPROMSUPPORT */


int main( void )
{
	uint8_t nSensors, i;
	int16_t decicelsius;
	uint8_t error;

	uart_init((UART_BAUD_SELECT((BAUD),F_CPU)));

#ifndef OW_ONE_BUS
	ow_set_bus(&PINA,&PORTA,&DDRA,PA6);
#endif

	sei();

	uart_puts_P( NEWLINESTR "DS18X20 1-Wire-Reader Demo by Martin Thomas" NEWLINESTR );
	uart_puts_P(            "-------------------------------------------" );

	nSensors = search_sensors();
	uart_put_int( (int)nSensors );
	uart_puts_P( " DS18X20 Sensor(s) available:" NEWLINESTR );

#if DS18X20_VERBOSE
	for (i = 0; i < nSensors; i++ ) {
		uart_puts_P("# in Bus :");
		uart_put_int( (int)i + 1);
		uart_puts_P(" : ");
		DS18X20_show_id_uart( &gSensorIDs[i][0], OW_ROMCODE_SIZE );
		uart_puts_P( NEWLINESTR );
	}
#endif

	for ( i = 0; i < nSensors; i++ ) {
		uart_puts_P( "Sensor# " );
		uart_put_int( (int)i+1 );
		uart_puts_P( " is a " );
		if ( gSensorIDs[i][0] == DS18S20_FAMILY_CODE ) {
			uart_puts_P( "DS18S20/DS1820" );
		} else if ( gSensorIDs[i][0] == DS1822_FAMILY_CODE ) {
			uart_puts_P( "DS1822" );
		}
		else {
			uart_puts_P( "DS18B20" );
		}
		uart_puts_P( " which is " );
		if ( DS18X20_get_power_status( &gSensorIDs[i][0] ) == DS18X20_POWER_PARASITE ) {
			uart_puts_P( "parasite" );
		} else {
			uart_puts_P( "externally" );
		}
		uart_puts_P( " powered" NEWLINESTR );
	}

#if DS18X20_EEPROMSUPPORT
	if ( nSensors > 0 ) {
		eeprom_test();
	}
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

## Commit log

2013-03-02 Dokumentation zum MKBoard und der H-Brücke hinzugefügt, Firmware Stub angelegt
    [H-Bridge.brd, H-Bridge.sch]
2013-03-03 avr firmware um stub für UART Kommunikation erweitert
2013-03-03 unnötiges uart_addon entfernt
2013-03-04 Treiber und Firmware erweitert
2013-04-06 one wire libs von Martin Thomas in AVR firmware hinzugefügt
2013-04-15 UART timing Problme mit ISR gefixed
2013-04-15 Master Makefile und dependencies angelegt
2013-04-18 PT100 Summe über 64 samples, Messung von 95°C -> -5°C aufgenommen
2013-04-19 Versuch der Anpassung an Messung 3, muss noch erweitert werden da timestamp nicht passt
2013-04-21 restructured PT100 calibration scripts
2013-10-18 fuses hinzugefügt
2013-10-24 Update of driver Makefile for libconfig++. Added save to cfg in driver class
2013-10-24 fix Makefile for driver, added cBrautomat class to GUI
2013-10-24 PT100 calibration verschoben
2013-10-24 MaxSteps auf 10 erhoeht, bugfixes
    [cBrautomat.cpp, main.c]
2013-10-26 einige Getter und Setter für Statusrückmeldung implementiert
2013-10-27 firmware, driver und GUI um Rührwerksansteuerung erweitert. Logfile mit Timestamp anlegen
2013-10-27 bugfix motor shutdown
2013-10-27 Tempprofile aus GUI einstellbar
    [temp_profile.cfg]
2013-10-28 Makefile überarbeitet, GUI Schrittweiterschaltung korrigiert, add remaining time
    [main.c]
2013-11-05 erster Versuch mit Bielmeier Einkochtopf
    [temp_profile.cfg]
2013-11-06 Schematic und Board vom modifizierten Programmer hinzugefügt
    [USBasp1_3.brd, USBasp1_3.sch]
2013-11-16 BoxStyle GTK
    [temp_profile.cfg]
2014-01-14 added 3 CAD exports
2015-04-30 Add Spülomat drawing
    [spuelomat.dxf]
2015-05-02 Spuelomat: Box eingezeichnet
    [spuelomat.dxf]
2018-09-20 neues Temperaturprofil
    [temp_profile.cfg, temp_profile_dunkler_Bock.cfg]
2018-09-20 Bild des Rührwerks hinzugefügt
    [temp_profile.cfg]

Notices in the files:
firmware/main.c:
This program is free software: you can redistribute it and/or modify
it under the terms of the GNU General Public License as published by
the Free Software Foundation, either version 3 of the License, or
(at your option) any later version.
